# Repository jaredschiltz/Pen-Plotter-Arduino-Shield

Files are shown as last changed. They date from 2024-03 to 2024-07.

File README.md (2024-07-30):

# Pen-Plotter-Arduino-Shield

## This is a Pen Plotter Arduino Shield to be used with an Uno R3 Arduino. Rev A

This shield is designed to work with an Arduino that has been loaded with GRBL 0.9. All electrical pin definitions are the default pin assignments specified in the 0.9 version of the code. N.B, servo PWM control uses PIN D11 (the Z-Limit signal). Pen-up command is M03 S255 and Pen-down command is M03 S0. With the current firmware, the angle delta between S255 and S0, is 90 degrees. A couple notes about this shield:

- This shield is a modification of the original CNC shield. There is no Z-axis motor control. An AGFRC A20CLS servo is being used to move the pen up and down. This high torque (7.5 kg-cm) servo runs on a voltage between 4.8 Volts and 8.4 Volts. To generate a 5.0 servo voltage, from the 12 V stepper motor power supply, a LM2596 buck switching regulator is used. The maximum 3 A output is enough to adequately drive the A20CLS motor. I was unable to find a maximum stall current specification for this particular servo, but the assumption is that it is a least an amp.
- The Y-axis is driven by two mirrored stepper motors, so this shield ties these control signals together on the board, rather than using a jumper. This saves some board space.
- Change glass fuse to PPTC resettable fuse. Fuse specs: 16 V, 8 A hold, 13.6 A trip
- Remove 10K pullup on enable signal. Each driver board has a built-in 20K pullup.
- Make limit switch connections 3 conductors, instead of 2 conductors. The OpenBuilds limit switches are a three wire interface.
- Remove jumper connections to EN, STEPS, DIRS. It is not necessary to expose these. Remove jumper connections to SPNEN, SPNDIR, COOLEN (these are unused by the pen plotter). Remove header to UART signals, SPI, and power connections. All of these removals will free up board space.
- Make mounting screw hole locations accessible.

The following changes should be made to Rev A:

- No changes need to be implemented to date

Parts list:
|Designator |Designation |MFG |MFG Part No. |Supplier|Supplier Part No. |Quantity|
|---|---|---|---|---|---|---|
|J3 |Vertical Connector Header, 2-Pos, 2.54 mm, 6 mm contact length |Wurth Elektronik |61300211121 |Digikey |732-5315-ND |1 |
|J4/J23,J22/J19,J20/J21|Vertical Connector Header, 2-Pos, 2.54 mm, 6 mm contact length |Wurth Elektronik |61300421121 |Digikey |732-5294-ND |3 |
|D1 |1N5824 5 A Schottky Diode |Vishay |SB520-E3/54 |Digikey |SB520-E3/54GICT-ND |1 |
|C2,C1,C3 |100uF 50 V |Panasonic |EEU-FM1H101B |Digikey |P19712CT-ND |3 |
|J6,J2,J1,J10,J7,J9 |8 Position Header Connector 0.100" (2.54mm) Through Hole |Sullins Connector Solutions|PPTC081LFBN-RC |Digikey |S7006-ND |6 |
|J5,J8,J11 |Vertical Connector Header, 4-Pos, 2.54 mm, 6 mm contact length |Wurth Elektronik |61300411121 |Digikey |732-5317-ND |3 |
|U1 |IC REG BUCK LM2596 5V 3A TO263-5 |UMW |LM2596S-5.0 |Digikey |4518-LM2596S-5.0CT-ND |1 |
|C5,C4 |330 uF, 50V, Low-ESR 58 m-ohm |Kemet |ESW337M050AH4EA |Digikey |399-6661-1-ND |2 |
|L1 |33 uH, 3.6 A, 51 m-Ohm |Abracon LLC |AIUR-06-330K |Digikey |AIUR-06-330K-ND |1 |
|J13 |2 Position Wire to Board Terminal Block Horizontal with Board 0.197" (5.00mm) Through Hole|Wurth Elektronik |691137710002 |Digikey |732-10955-ND |1 |
|J14,J15,J16,J12,J17 |Vertical Connector Header, 3-Pos, 2.54 mm, 6 mm contact length |Wurth Elektronik |61300311121 |Digikey |732-5316-ND |5 |
|J18 |Vertical Connector Header, (2 Rows / 6-Pos), 2.54 mm, 6 mm contact length |Wurth Elektronik |61300621121 |Digikey |732-5295-ND |1 |
|U3 |Vertical Connector Header, 6-Pos, 2.54 mm, 6 mm contact length |Wurth Elektronik |61300611121 |Digikey |732-5319-ND |1 |
|U2, U7 |Vertical Connector Header, 8-Pos, 2.54 mm, 6 mm contact length |Wurth Elektronik |61300811121 |Digikey |732-5321-ND |1 |
|U6 |Vertical Connector Header, 10-Pos, 2.54 mm, 6 mm contact length |Wurth Elektronik |61301011121 |Digikey |732-2670-ND | |
|F1 |PPTC Radial Resettable Fuse (8.0 A Hold Current, 13.5 A Trip Current, 16 V Max) |RFE/Fuzetec |FRG800-16F |Digikey |3451-FRG800-16F-ND |1 |
|S1 |MOMENTARY-SWITCH-SPST-PTH-6.0MM |CUI Devices |TS02-66-60-BK-160-LCR-D|Digikey |2223-TS02-66-60-BK-160-LCR-D-ND|1 |
|H3 |M3 Mounting Hole | | | | |1 |

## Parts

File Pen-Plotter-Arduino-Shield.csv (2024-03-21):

Id | Designator | Footprint | Quantity | Designation | Supplier and ref
1 | J23,J22,J19,J20,J4,J21,J3 | 1X02_LOCK | 7 | CONN_02LOCK
2 | D1 | D_DO-201AD_P15.24mm_Horizontal | 1 | 1N5822
3 | C2,C1,C3 | CPOL-RADIAL-5MM-10MM | 3 | 100uF
4 | J6,J2,J1,J10,J7,J9 | 1X08_LOCK | 6 | CONN_08LOCK
5 | J5,J8,J11 | 1X04_LOCK | 3 | CONN_04LOCK
6 | U1 | TO-263-5_TabPin3 | 1 | LM2596S-5
7 | C5,C4 | CPOL-RADIAL-5MM-10MM | 2 | 330uF
8 | L1 | INDRD750W80D1350H1800 | 1 | 33uH
9 | J13 | 691137710002 | 1 | 691137710002
10 | J14,J15,J16,J12,J17 | 1X03_LOCK | 5 | CONN_03LOCK
11 | H1 | Arduino_MountingHole | 1 | MountingHole1
12 | U7 | Arduino_PinSocket_1x08_P2.54mm_Vertical | 1 | Digital_2
13 | U6 | Arduino_PinSocket_1x10_P2.54mm_Vertical | 1 | Digital_1
14 | H4 | Arduino_MountingHole | 1 | MountingHole4
15 | J18 | 2X3 | 1 | CONN_03X2FEMALE
16 | U3 | Arduino_PinSocket_1x06_P2.54mm_Vertical | 1 | Analog_2
17 | U2 | Arduino_PinSocket_1x08_P2.54mm_Vertical | 1 | Analog_1
18 | F1 | FRG800-16F | 1 | Polyfuse
19 | H2 | Arduino_MountingHole | 1 | MountingHole2
20 | S1 | TACTILE_SWITCH_PTH_6.0MM | 1 | MOMENTARY-SWITCH-SPST-PTH-6.0MM
21 | H3 | Arduino_MountingHole | 1 | MountingHole3

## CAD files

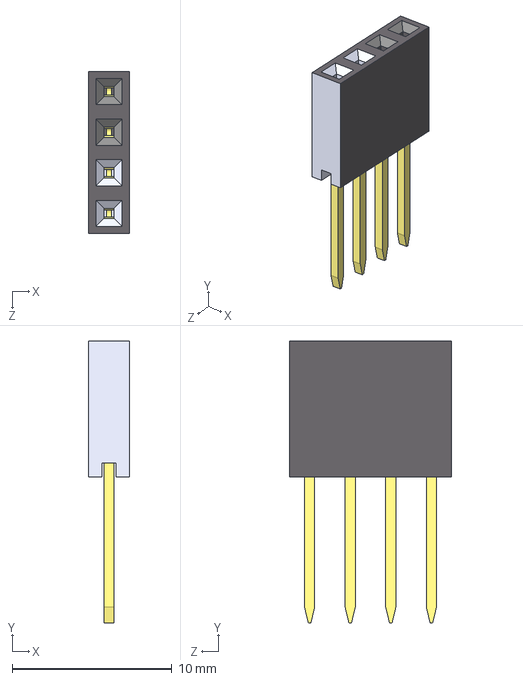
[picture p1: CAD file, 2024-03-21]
3DModels/1x4.STEP
2.54 x 17.6 x 10.2 mm

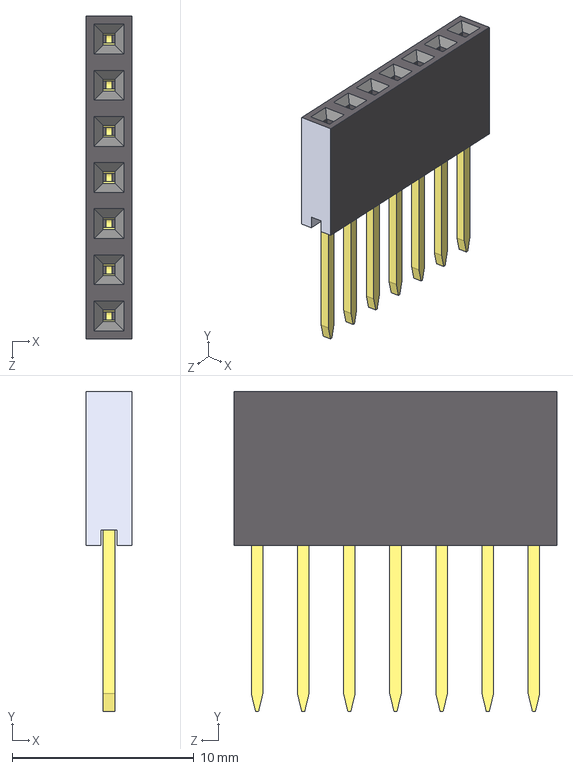
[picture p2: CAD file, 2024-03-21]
3DModels/1x7.STEP
2.54 x 17.6 x 17.8 mm

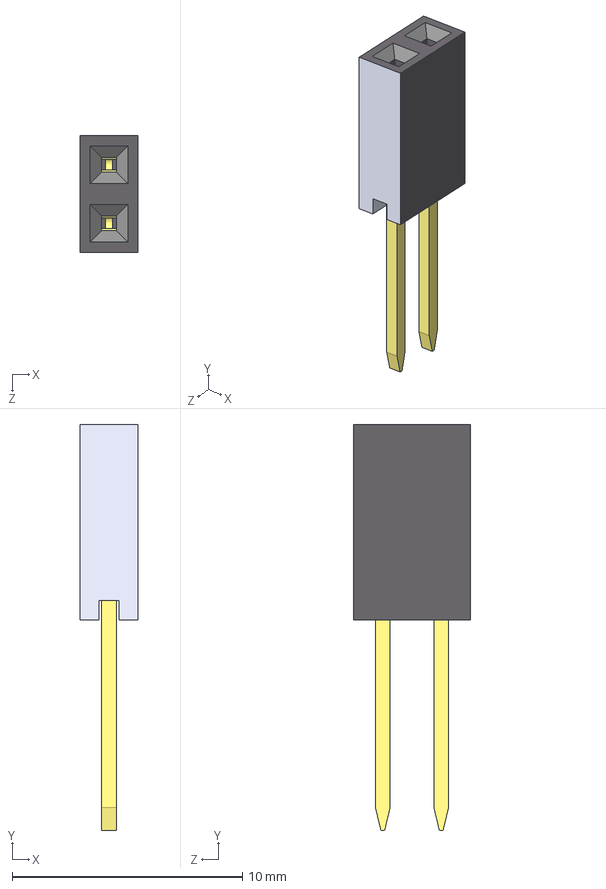
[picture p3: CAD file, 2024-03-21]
3DModels/1x2.STEP
2.54 x 17.6 x 5.08 mm

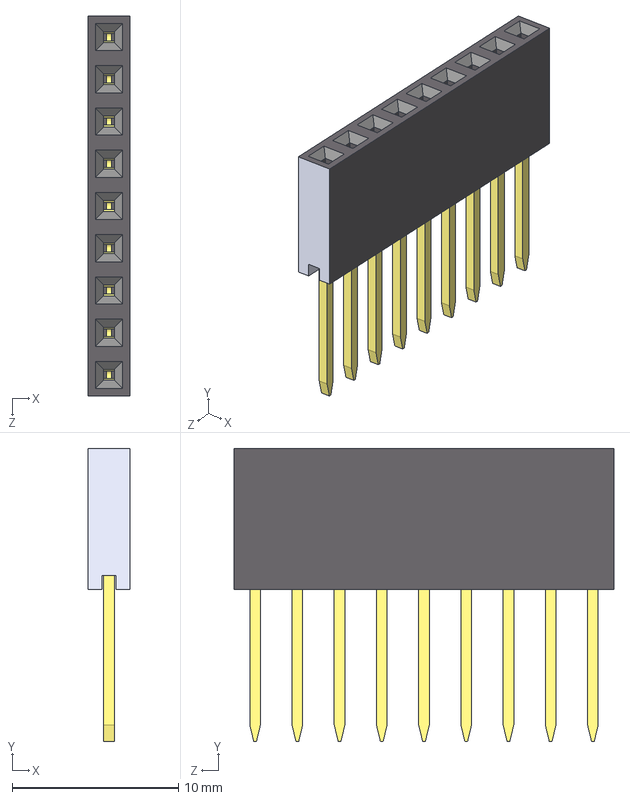
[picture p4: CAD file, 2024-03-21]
3DModels/1x9.STEP
2.54 x 17.6 x 22.9 mm

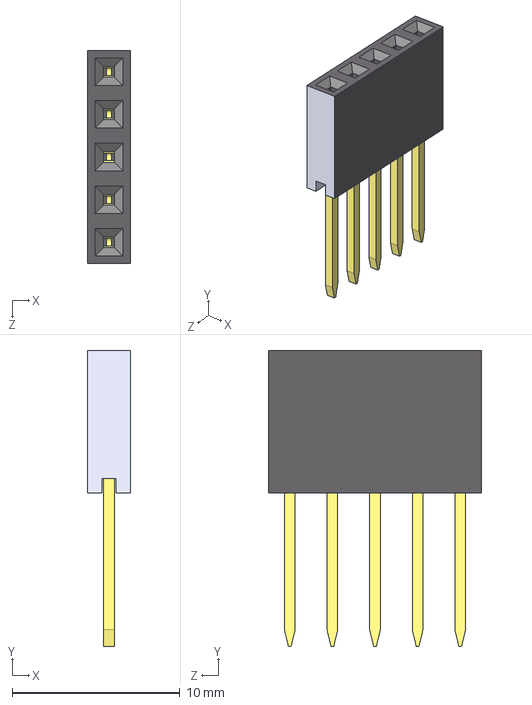
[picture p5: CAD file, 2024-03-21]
3DModels/1x5.STEP
2.54 x 17.6 x 12.7 mm

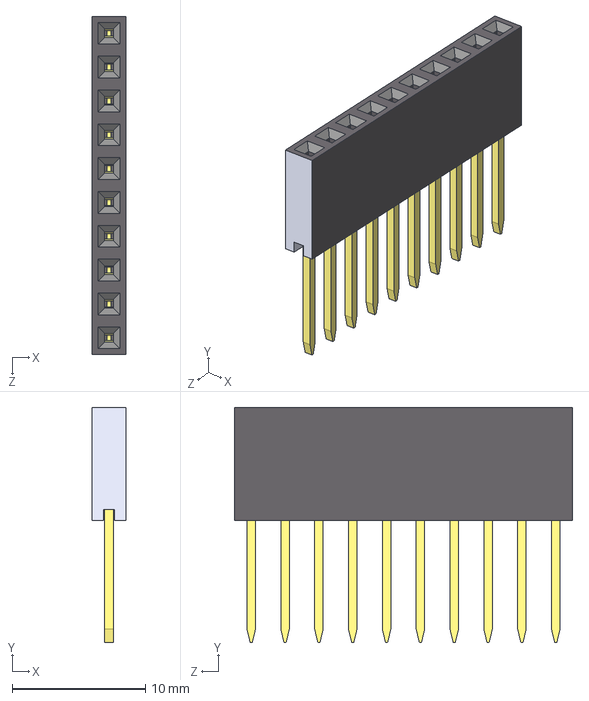
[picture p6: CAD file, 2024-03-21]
3DModels/1x10.STEP
2.54 x 17.6 x 25.4 mm

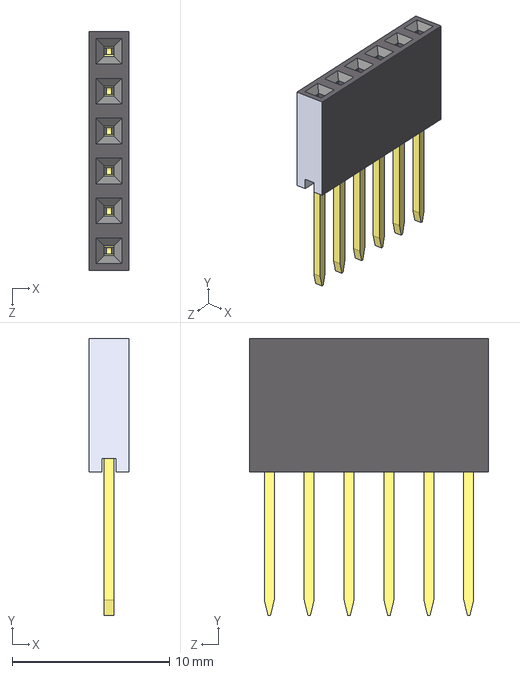
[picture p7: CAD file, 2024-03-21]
3DModels/1x6.STEP
2.54 x 17.6 x 15.2 mm

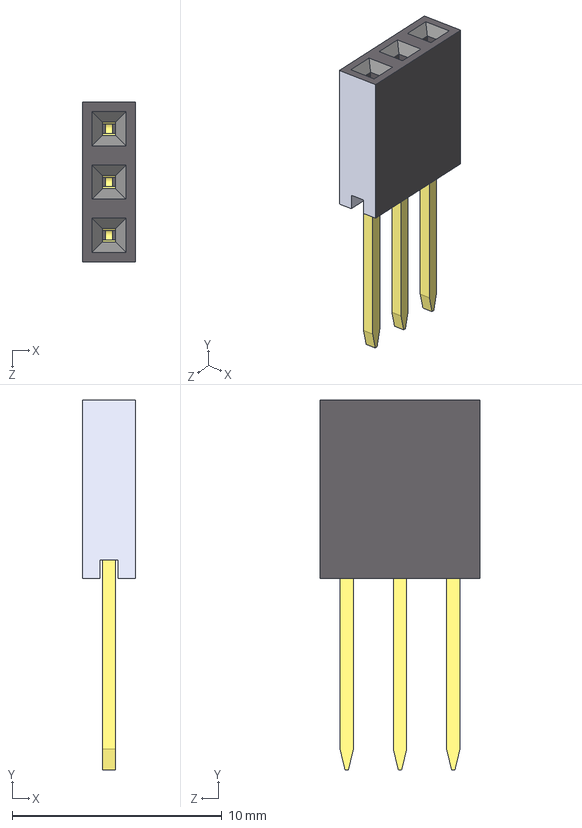
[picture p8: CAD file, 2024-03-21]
3DModels/pin header female 2.54mm_0.1in.STEP
2.54 x 17.6 x 7.62 mm

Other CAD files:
3DModels/pin_header_female_2.54mm_0.1in.STEP

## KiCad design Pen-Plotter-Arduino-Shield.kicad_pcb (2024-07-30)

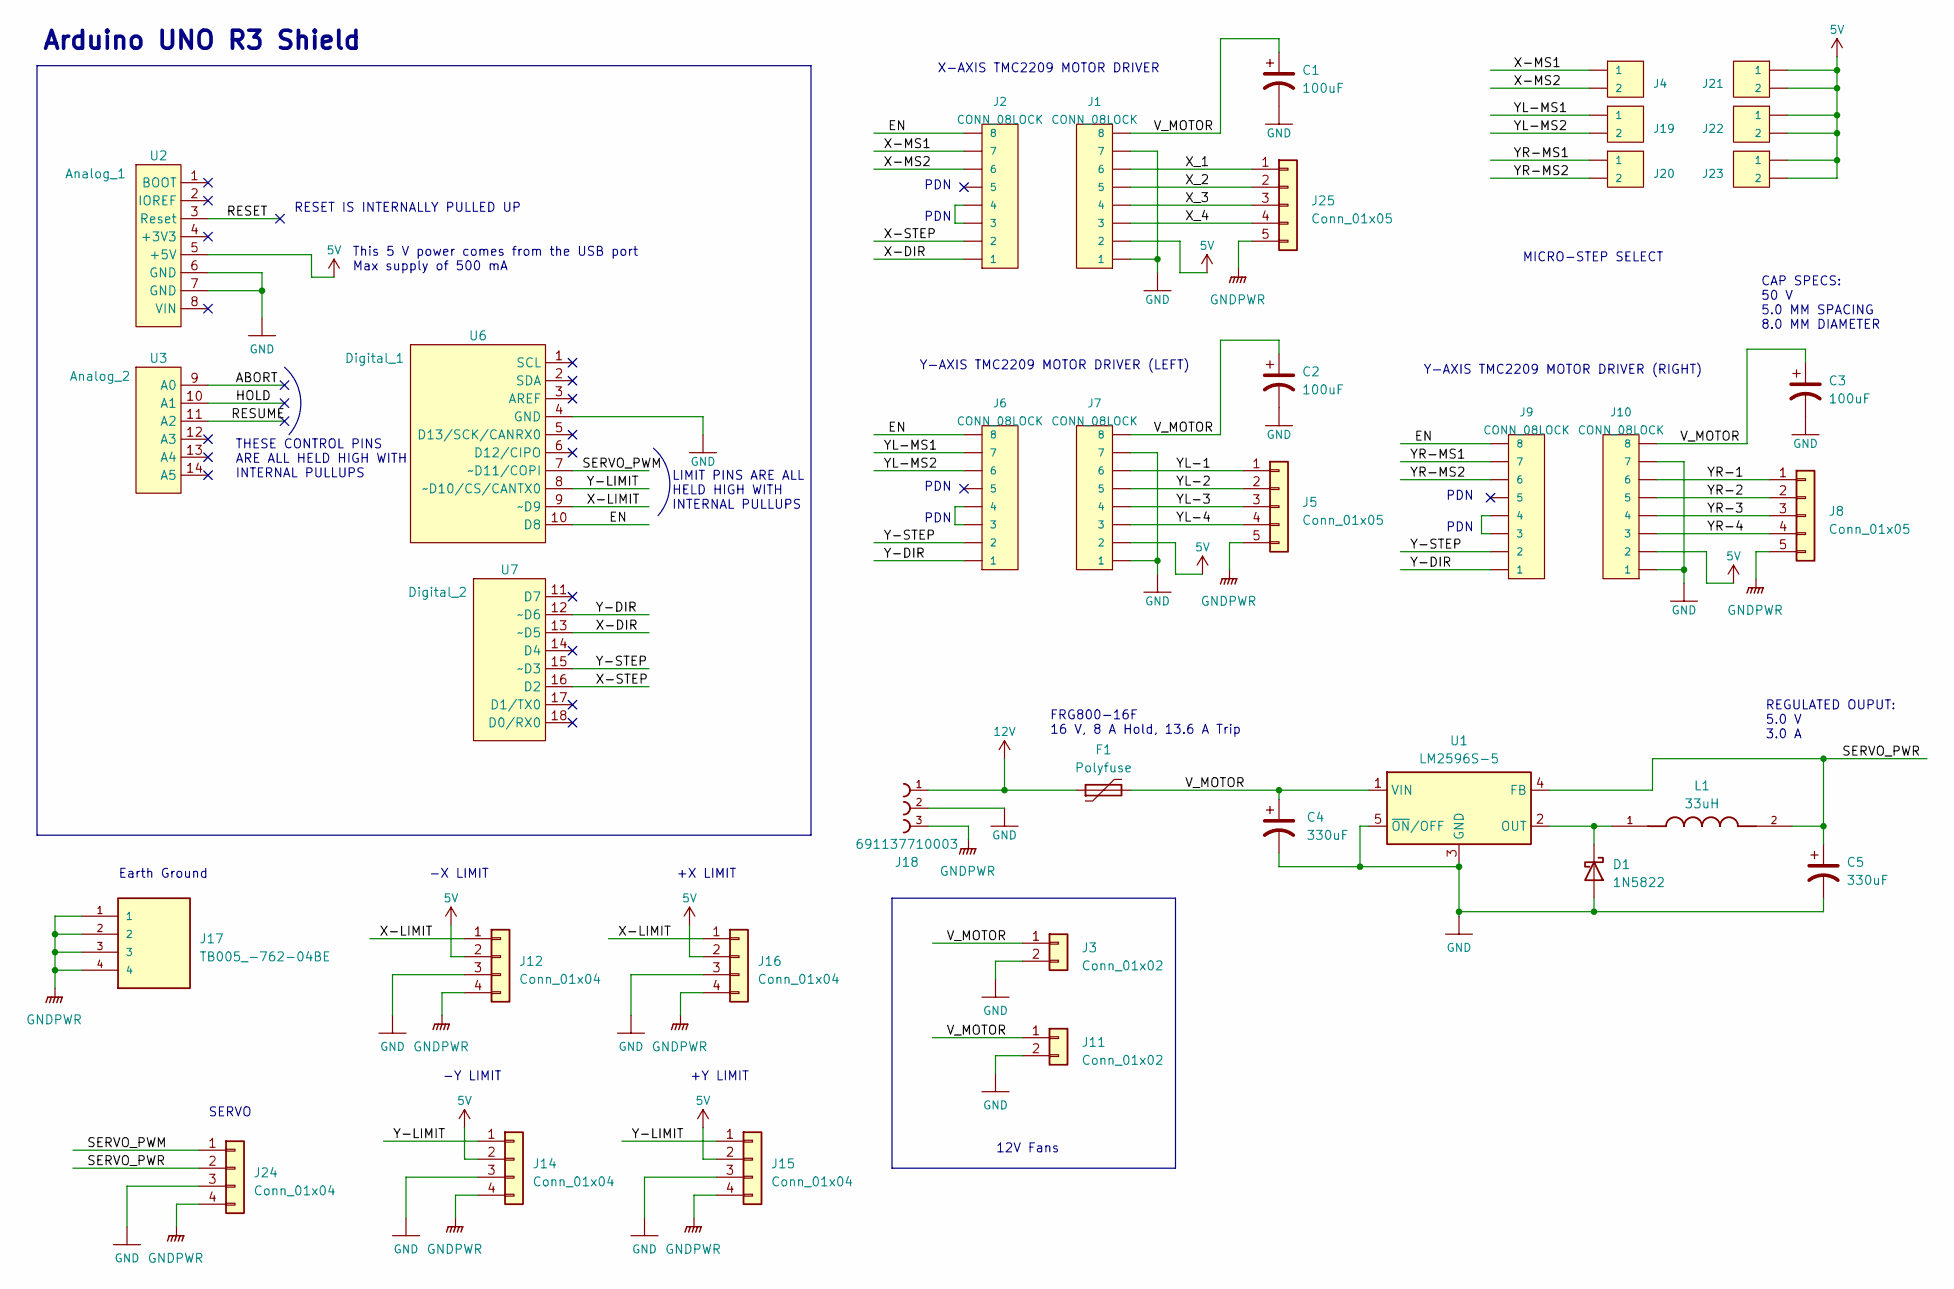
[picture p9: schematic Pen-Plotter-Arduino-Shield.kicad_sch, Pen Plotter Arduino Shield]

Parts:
C1, C2, C3: 100uF; CPOL-RADIAL-5MM-10MM
C4, C5: 330uF; CPOL-RADIAL-5MM-10MM
D1: 1N5822; D_DO-201AD_P15.24mm_Horizontal
F1: Polyfuse; FRG800-16F
J1, J2, J6, J7, J9, J10: CONN_08LOCK; 1X08_LOCK
J3, J11: Conn_01x02; JST_XH_B2B-XH-A_1x02_P2.50mm_Vertical
J4, J19, J20, J21, J22, J23: CONN_02LOCK; 1X02_LOCK
J5, J8, J25: Conn_01x05; JST_XH_B5B-XH-A_1x05_P2.50mm_Vertical
J12, J14, J15, J16, J24: Conn_01x04; JST_XH_B4B-XH-A_1x04_P2.50mm_Vertical
J17: TB005_-762-04BE; CUI_TB005 -762-04BE; DigiKey_Part_Number TB005-762-04BE-ND
J18: 691137710003
L1: 33uH; INDRD750W80D1350H1800; PARTREV 6/23/2022
U1: LM2596S-5; TO-263-5_TabPin3
U2: Analog_1; Arduino_PinSocket_1x08_P2.54mm_Vertical
U3: Analog_2; Arduino_PinSocket_1x06_P2.54mm_Vertical
U6: Digital_1; Arduino_PinSocket_1x10_P2.54mm_Vertical
U7: Digital_2; Arduino_PinSocket_1x08_P2.54mm_Vertical

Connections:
5V: J1.2, J7.2, J10.2, J12.2, J14.2, J15.2, J16.2, J21.1, J21.2, J22.1, J22.2, J23.1, J23.2, U2.5 (+5V)
12V: F1.1, J18.1
/ABORT: U3.9 (A0)
/EN: J2.8, J6.8, J9.8, U6.10 (D8)
/HOLD: U3.10 (A1)
/RESET: U2.3 (Reset)
/RESUME: U3.11 (A2)
/SERVO_PWM: J24.1, U6.7 (~D11/COPI)
/SERVO_PWR: C5.1, J24.2, L1.2, U1.4 (FB)
/V_MOTOR: C1.1, C2.1, C3.1, C4.1, F1.2, J1.8, J3.1, J7.8, J10.8, J11.1, U1.1 (VIN)
/X-DIR: J2.1, U7.13 (~D5)
/X-LIMIT: J12.1, J16.1, U6.9 (~D9)
/X-MS1: J2.7, J4.1
/X-MS2: J2.6, J4.2
/X-STEP: J2.2, U7.16 (D2)
/X_1: J1.6, J25.1
/X_2: J1.5, J25.2
/X_3: J1.4, J25.3
/X_4: J1.3, J25.4
/Y-DIR: J6.1, J9.1, U7.12 (~D6)
/Y-LIMIT: J14.1, J15.1, U6.8 (~D10/CS/CANTX0)
/Y-STEP: J6.2, J9.2, U7.15 (~D3)
/YL-1: J5.1, J7.6
/YL-2: J5.2, J7.5
/YL-3: J5.3, J7.4
/YL-4: J5.4, J7.3
/YL-MS1: J6.7, J19.1
/YL-MS2: J6.6, J19.2
/YR-1: J8.1, J10.6
/YR-2: J8.2, J10.5
/YR-3: J8.3, J10.4
/YR-4: J8.4, J10.3
/YR-MS1: J9.7, J20.1
/YR-MS2: J9.6, J20.2
GND: C1.2, C2.2, C3.2, C4.2, C5.2, D1.2 (A), J1.1, J1.7, J3.2, J7.1, J7.7, J10.1, J10.7, J11.2, J12.3, J14.3, J15.3, J16.3, J18.2, J24.3, U1.3 (GND), U1.5 (~ON/OFF), U2.6 (GND), U2.7 (GND), U6.4 (GND)
GNDPWR: J5.5, J8.5, J12.4, J14.4, J15.4, J16.4, J17.1, J17.2, J17.3, J17.4, J18.3, J24.4, J25.5
unnamed: D1.1 (K), L1.1, U1.2 (OUT)
unnamed: J2.3, J2.4
unnamed: J6.3, J6.4
unnamed: J9.3, J9.4

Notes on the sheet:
THESE CONTROL PINS ARE ALL HELD HIGH WITH INTERNAL PULLUPS
RESET IS INTERNALLY PULLED UP
+X LIMIT
Y-AXIS TMC2209 MOTOR DRIVER (RIGHT)
FRG800-16F 16 V, 8 A Hold, 13.6 A Trip
-X LIMIT
X-AXIS TMC2209 MOTOR DRIVER
Arduino UNO R3 Shield
REGULATED OUPUT: 5.0 V 3.0 A
This 5 V power comes from the USB port Max supply of 500 mA
+Y LIMIT
12V Fans
PDN
CAP SPECS: 50 V 5.0 MM SPACING 8.0 MM DIAMETER
Earth Ground
MICRO-STEP SELECT
Y-AXIS TMC2209 MOTOR DRIVER (LEFT)
SERVO
-Y LIMIT
LIMIT PINS ARE ALL HELD HIGH WITH INTERNAL PULLUPS

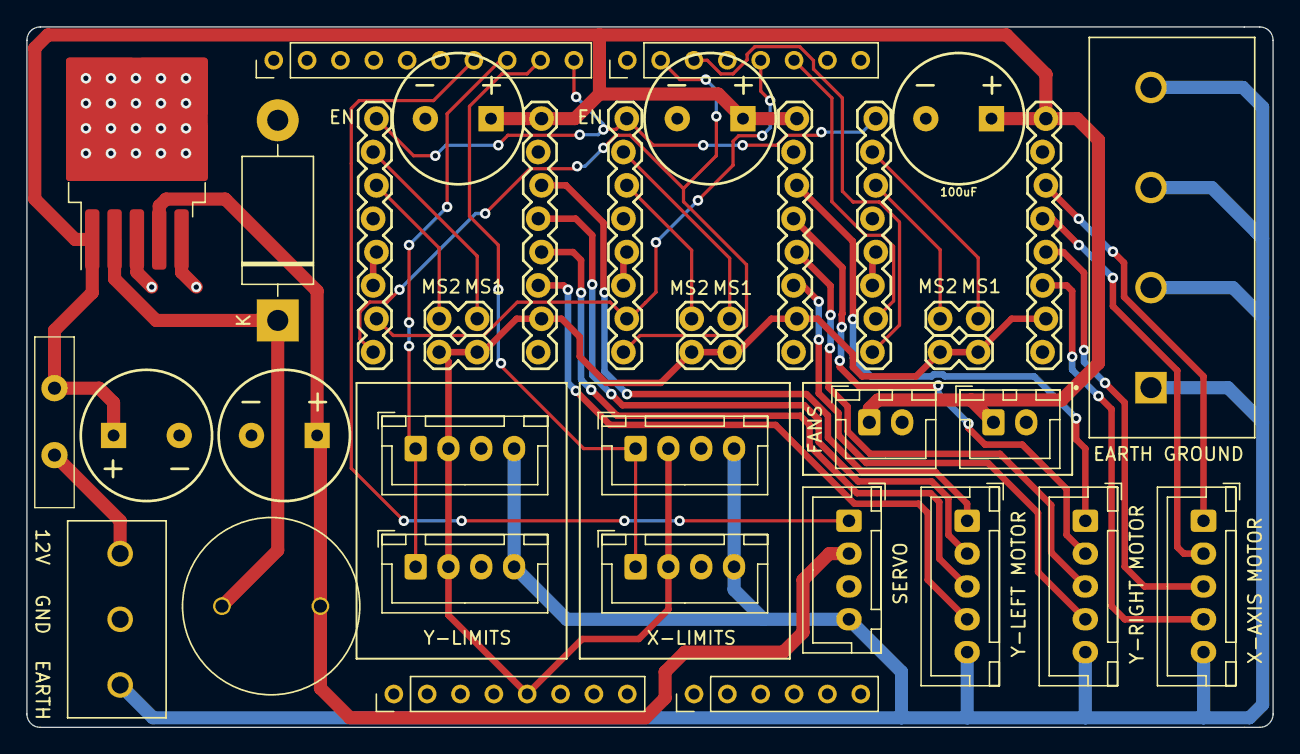
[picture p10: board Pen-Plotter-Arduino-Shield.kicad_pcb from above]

Board: 2 copper layers, 94.9 x 53.3 mm, 37 parts (0 on the bottom side), 36 nets.

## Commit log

2024-03-21 add source for rev-
    [1x10.STEP, 1x2.STEP, 1x4.STEP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]
2024-07-30 update all files to Revision A
    [Pen-Plotter-Arduino-Shield.kicad_pcb, Pen-Plotter-Arduino-Shield.kicad_sch]
